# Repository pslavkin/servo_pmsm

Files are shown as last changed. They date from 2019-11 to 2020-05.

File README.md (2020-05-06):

# PMSM Servo motor driver based on C2000 - PCB

> development of a customized high precision microcontrolled permament magnet embedded servo motor

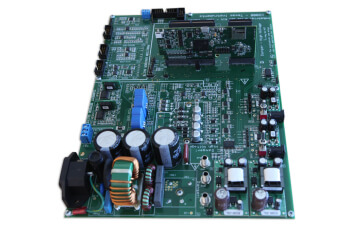
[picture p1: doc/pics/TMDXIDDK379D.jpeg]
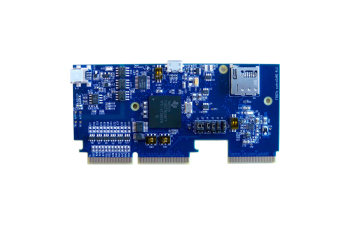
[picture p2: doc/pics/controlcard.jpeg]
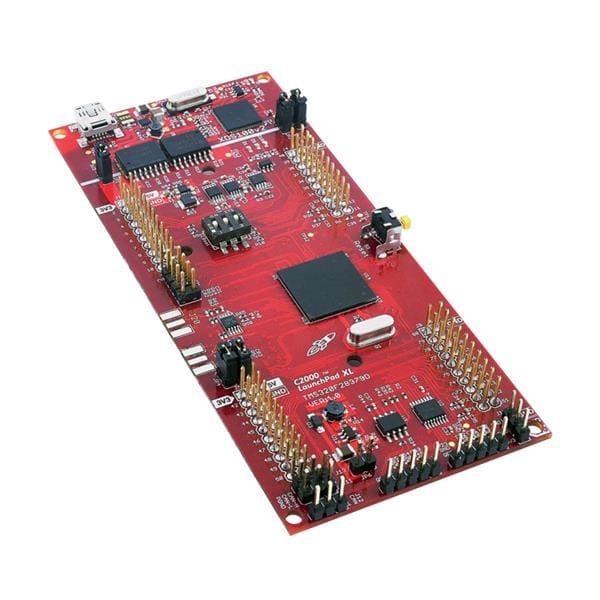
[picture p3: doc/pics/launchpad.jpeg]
   
## Progress
<!--- 
- ![rojo](https://placehold.it/15/FF0000/000000?text=+)
- ![amarillo](https://placehold.it/15/FFFF00/000000?text=+)
- ![azul](https://placehold.it/15/0000FF/000000?text=+)
- ![verde](https://placehold.it/15/00FF00/000000?text=+)
embedded gist
<img src="doc/pics/servo-15.jpg" width="800"/>
https://gist.github.com/rxaviers/7360908

- :heavy_check_mark: connected to a chinise CNC works!
- :red_circle:       Dual core interconnect IPC
-->
- :heavy_check_mark:    controller schematics from Altium to kicad
- :heavy_check_mark:    setting kicad libs, datasheet, remove unused IC's
- :heavy_check_mark:    mixing high power cirtuit to kicad
- :heavy_check_mark:    two servo motor control on same board aproach!
- :heavy_check_mark:    setting kicad libs, datasheet, remove unused IC's 
- :heavy_check_mark:    adc
- :heavy_check_mark:    igbt interface
- :heavy_check_mark:    lem measurement
- :heavy_check_mark:    ac input
- :heavy_check_mark:    connect interfaces to GPIO's (ecat0/1, enet, leds, etc)
- :heavy_check_mark:    shunt using isolated ADC fron/backend
- :heavy_check_mark:    isolated GPI for external switches and sensor on any polarity
- :heavy_check_mark:    8 channel buffer to drive IGBT
- :heavy_check_mark:    ac/dc -> dc/dc -> ldo for clean power supplies
- :heavy_check_mark:        Line voltage measurement
- :heavy_check_mark:        overcurrent protection using CMPSS
- :red_circle:          aborted! lem is better changing/adding shunt measurement with sigma deltas isolated ADC
- :heavy_check_mark:    LEM revival. I've decided to return to the idea of LEM 'cose sigma
  delta carry more complexity and less benefits. But SD could be included on power stage and
I'll let pins to aquire and filter it.
- :heavy_check_mark:     schematics ready!, and check rules passed. go to part numbering and
  footprint selection
- :red_circle:          isolated GPIO aborted! I've reise free pins that comes from IGBT
- :heavy_check_mark:    EVE LCD driven choosen as the UI by spi.. I's all the thinks we need
- :heavy_check_mark:    3d added EVE LCD 3. 20w offline ac/dc changed to 10w. 15vcold
  eliminated, two buttons eliminated. 2 LEM's eliminated
- :construction:        all footprints choosen, but deserves some comprobation
- :heavy_check_mark:    placement rought done
- :heavy_check_mark:    ronting..
- :heavy_check_mark:    moving ethernet connector to right and remove 15vh->5vh and debuh
- :heavy_check_mark:    ronting DONE!!! begin to improve nets..
- :heavy_check_mark:    Gerbers READY.. leaving Moldova...
- :heavy_check_mark:    Gerbers RELOADED from Bariloche
- :heavy_check_mark:    Gerbers RELEAED ... cross fingers..
- :heavy_check_mark:    Board partially manufactured!! miss uC that is traveling on a
  boat...see pics

## Welcome back Moldova 3.0

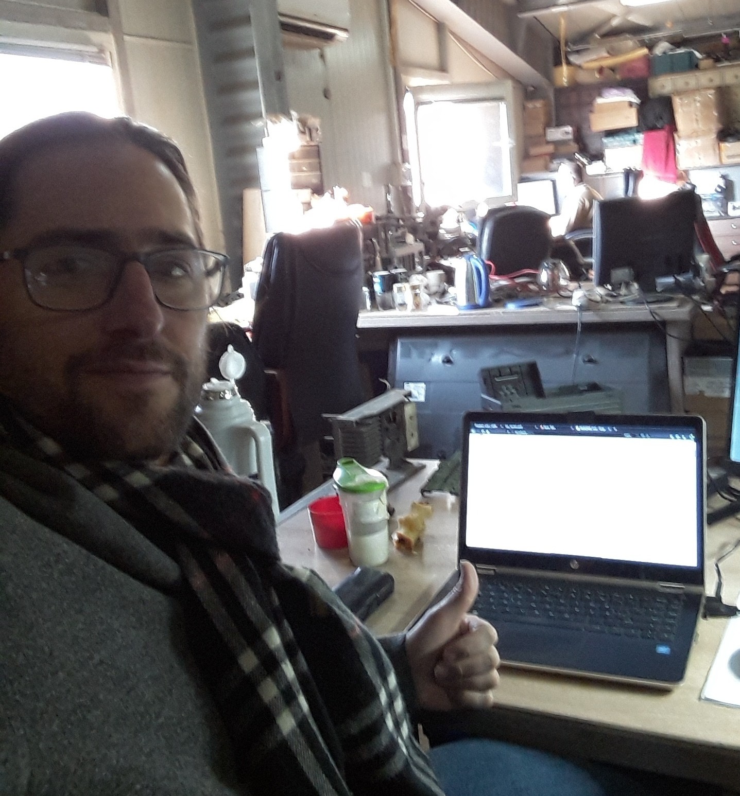
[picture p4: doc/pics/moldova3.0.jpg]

I've come back to finish PCB, there we are... sdarobia!

## Table of Contents

- [schematics](#schematics)
- [Contributing](#contributing)
- [Team](#team)
- [FAQ](#faq)
- [Support](#support)
- [Hierarchy](#hierarchy)
- [License](#license)
---
## schematics
There are the actual schematics generated until now:

## complete pdf link
[complete pdf schematic](./doc/pics/servo.pdf)

## Layout
Met's begin with layout!
first pic, easy, doesn't it?

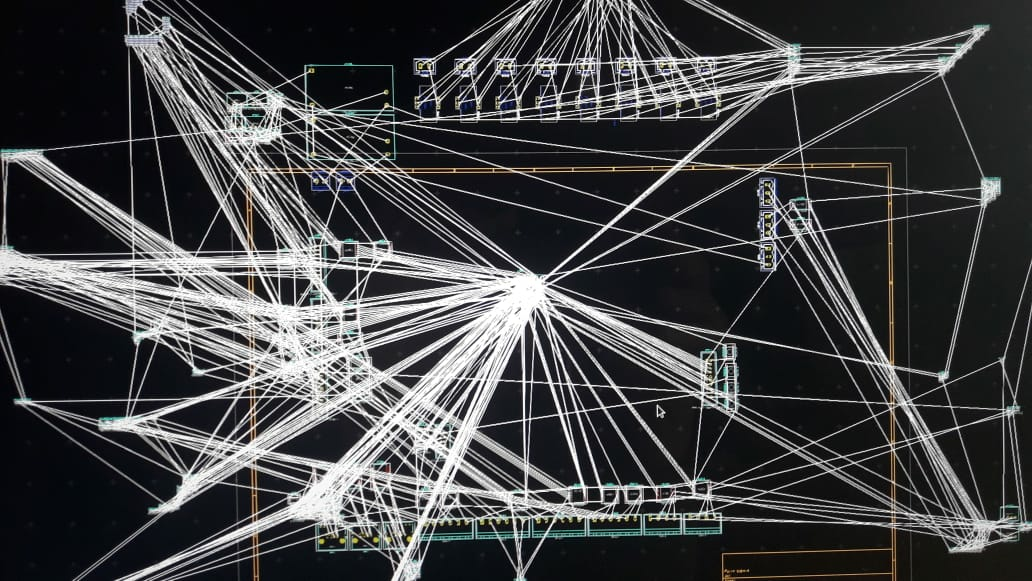
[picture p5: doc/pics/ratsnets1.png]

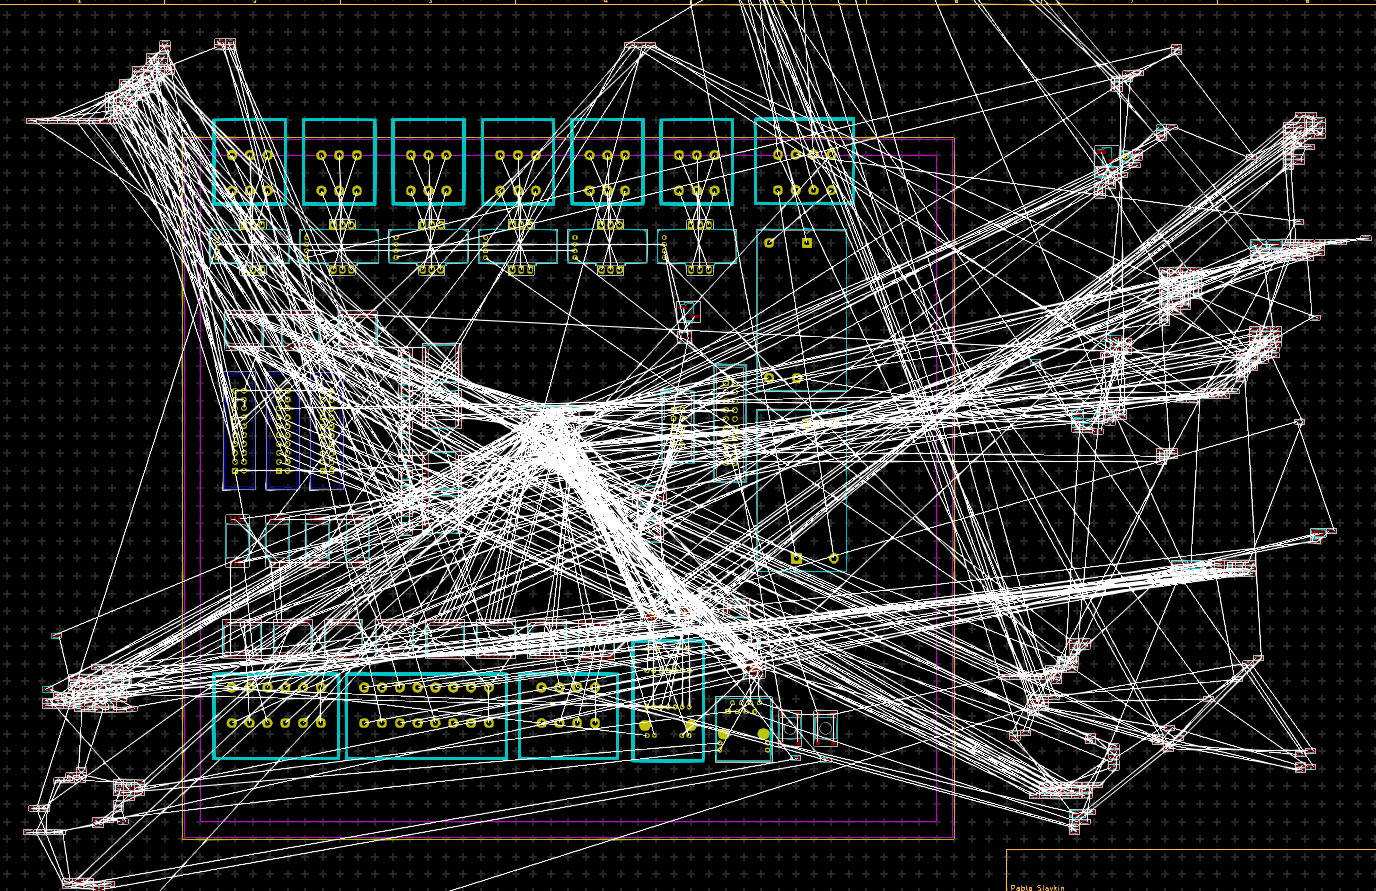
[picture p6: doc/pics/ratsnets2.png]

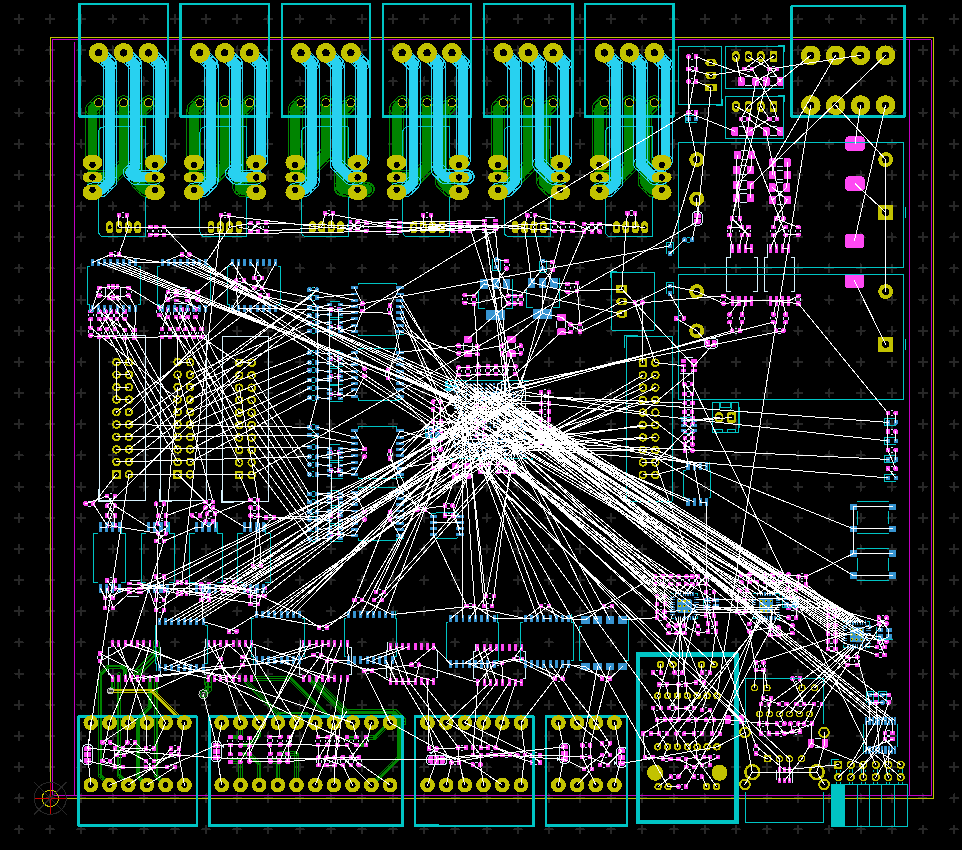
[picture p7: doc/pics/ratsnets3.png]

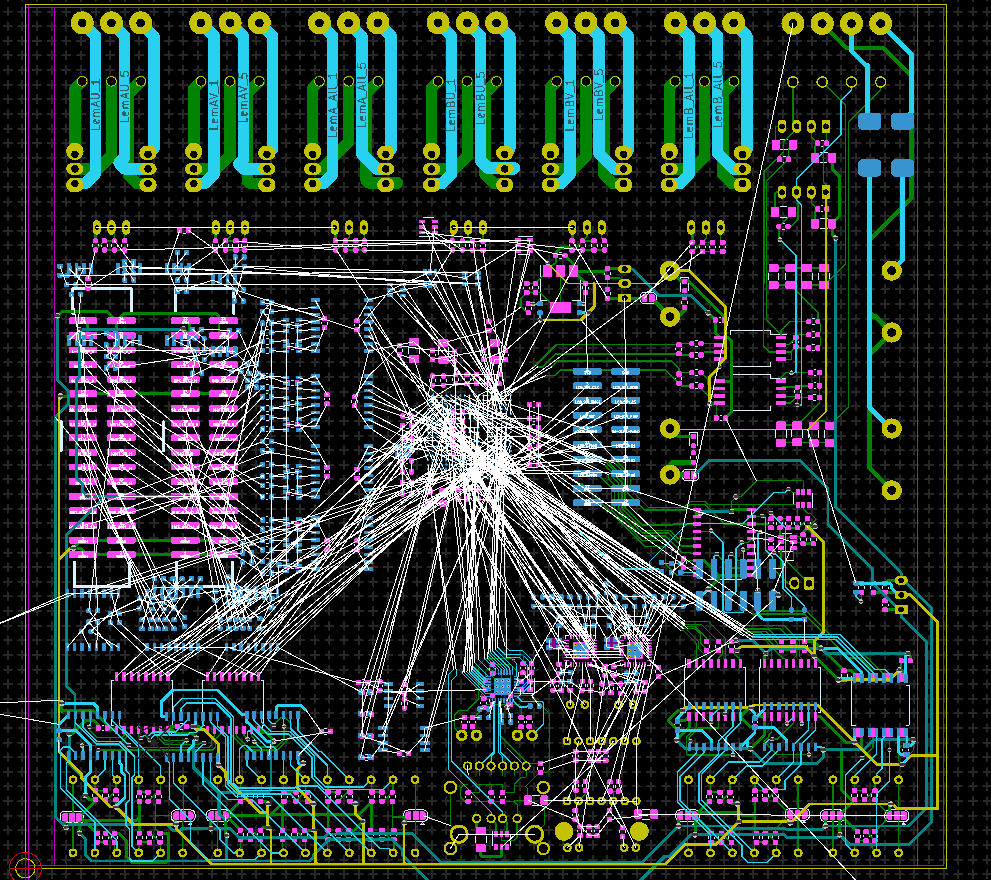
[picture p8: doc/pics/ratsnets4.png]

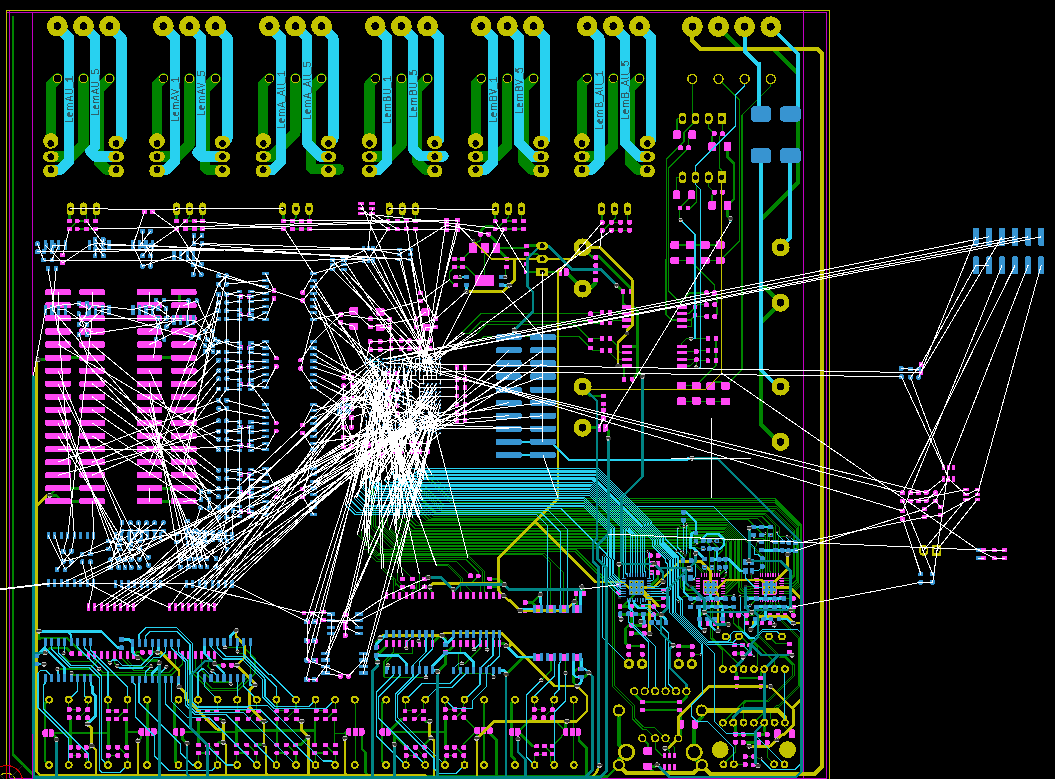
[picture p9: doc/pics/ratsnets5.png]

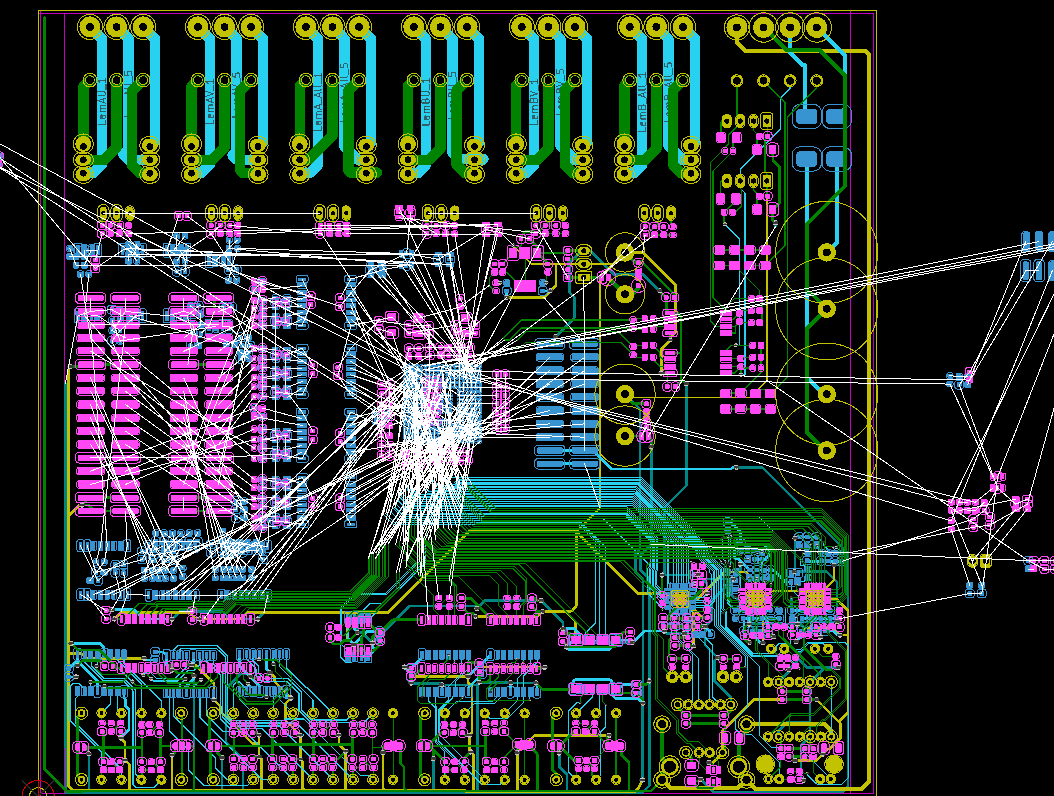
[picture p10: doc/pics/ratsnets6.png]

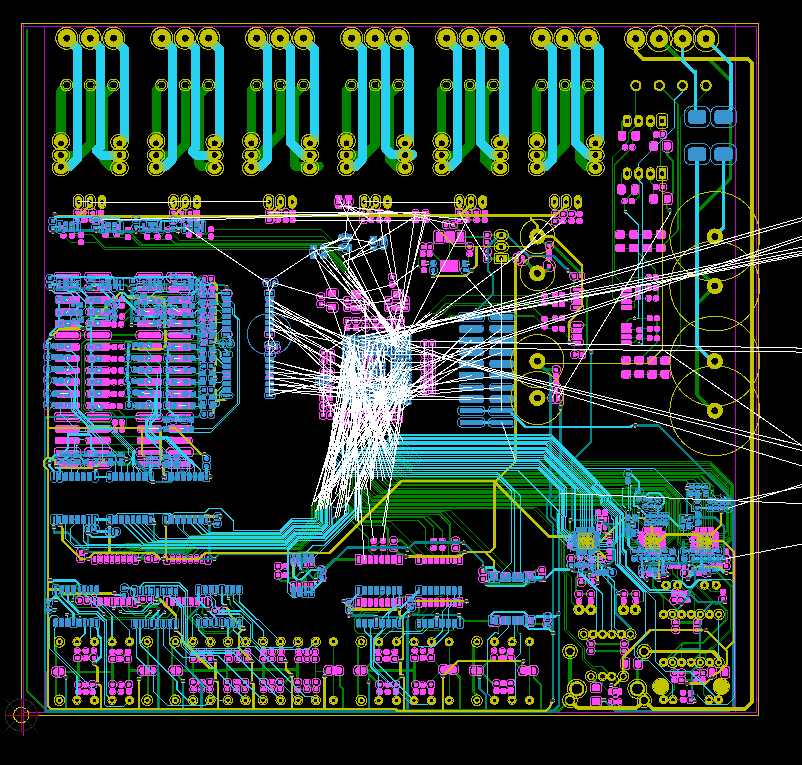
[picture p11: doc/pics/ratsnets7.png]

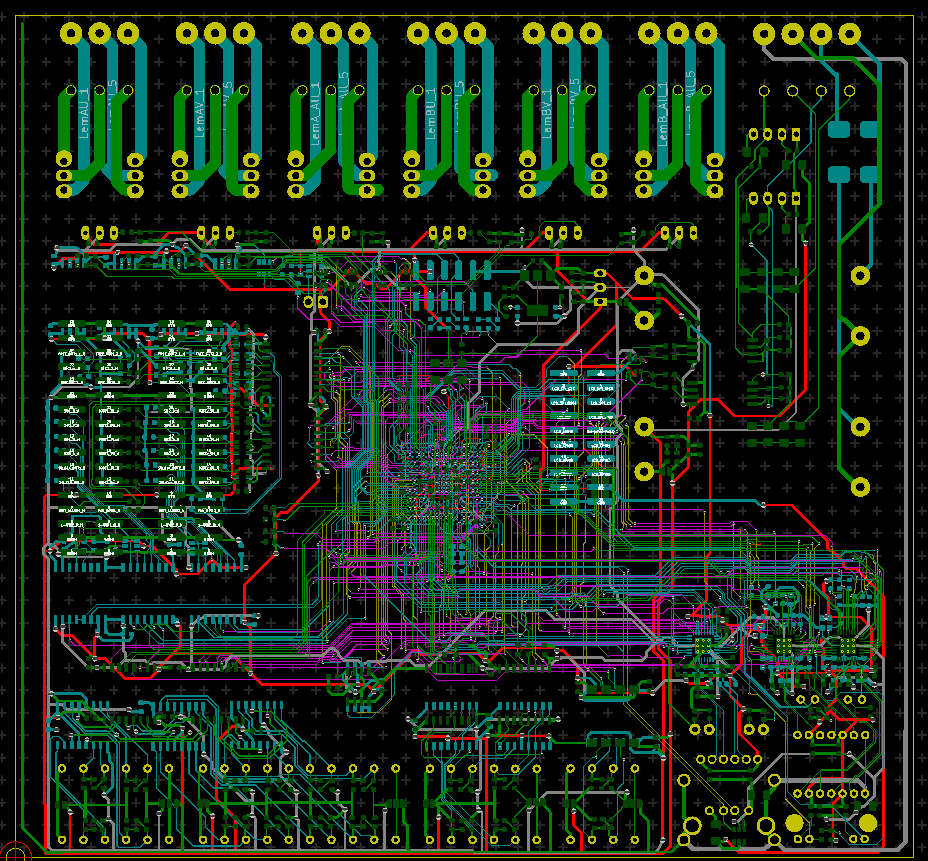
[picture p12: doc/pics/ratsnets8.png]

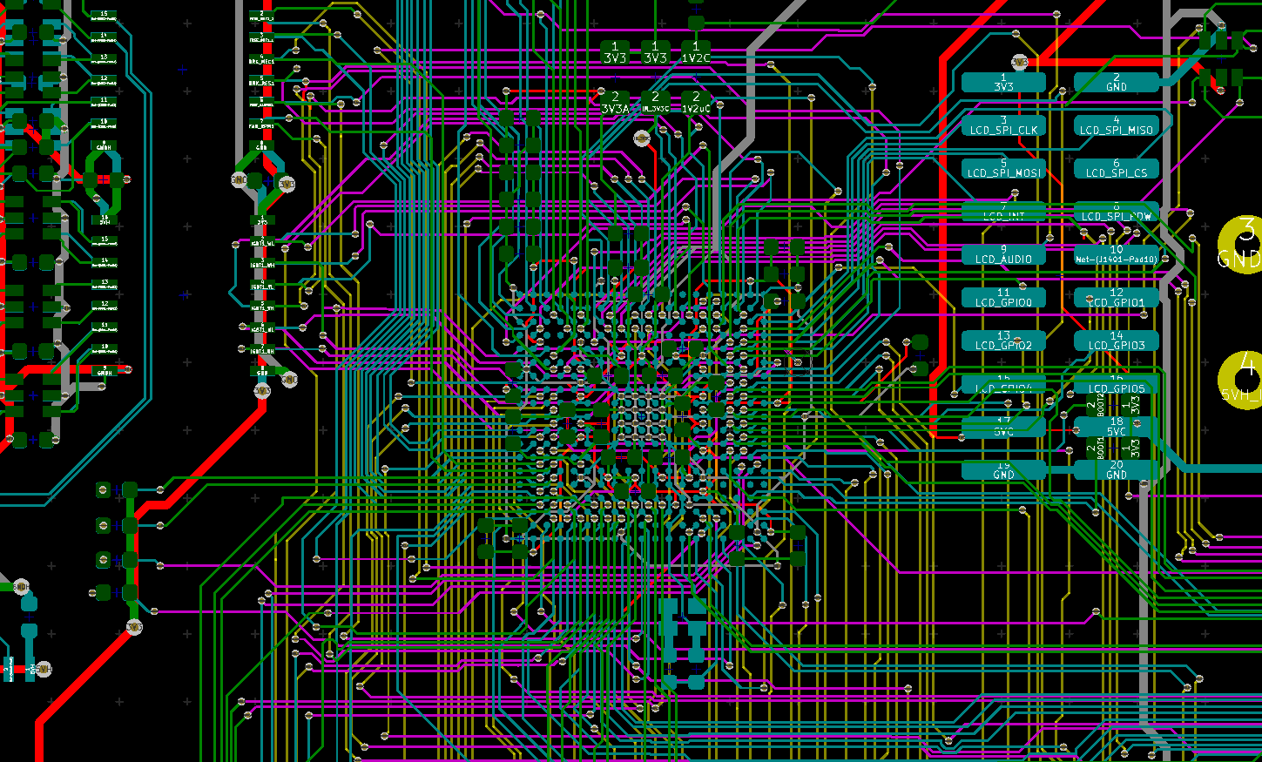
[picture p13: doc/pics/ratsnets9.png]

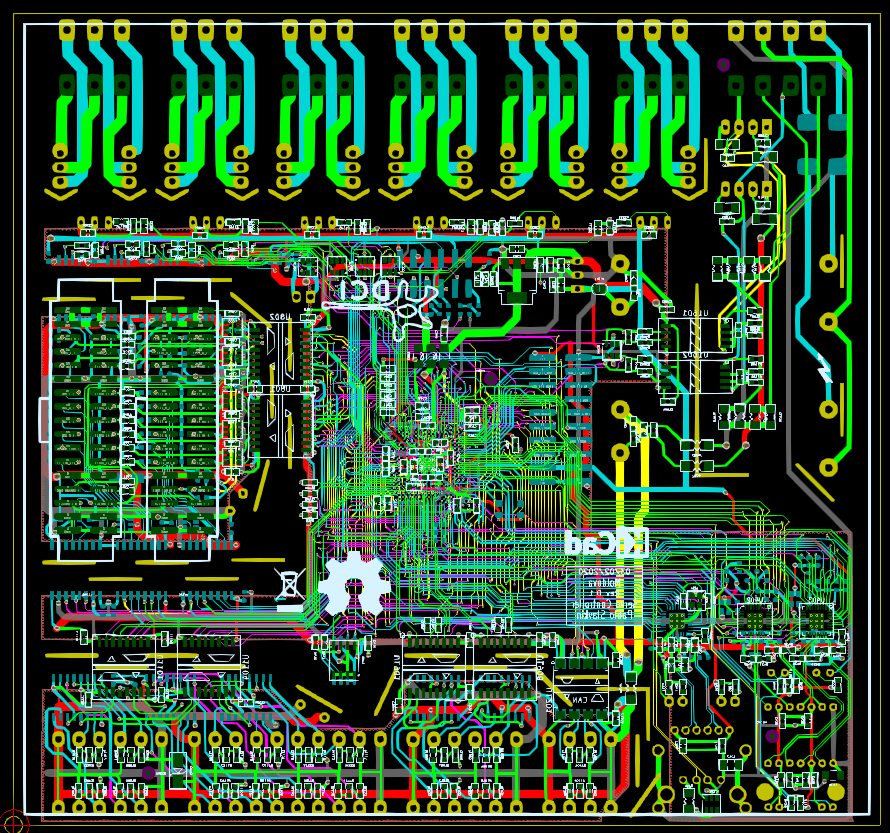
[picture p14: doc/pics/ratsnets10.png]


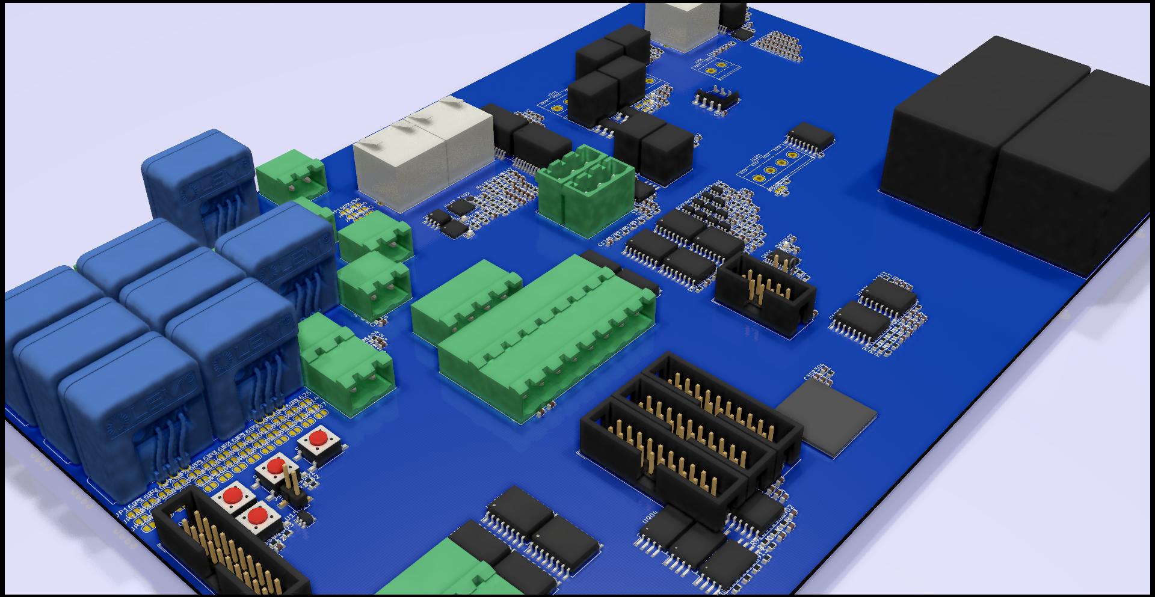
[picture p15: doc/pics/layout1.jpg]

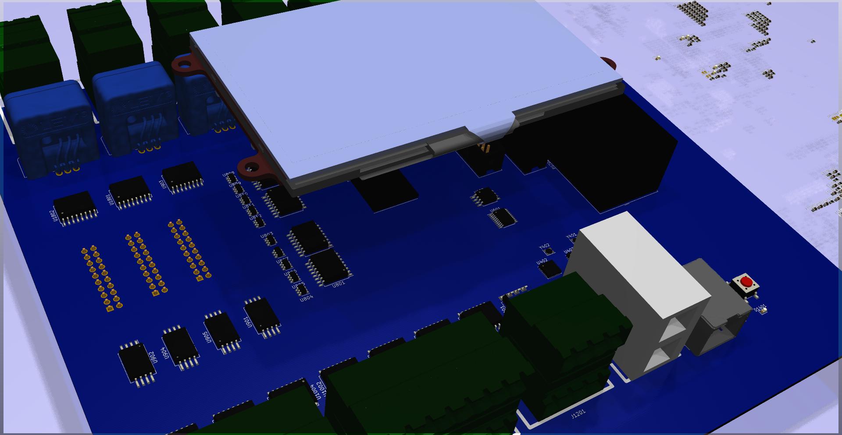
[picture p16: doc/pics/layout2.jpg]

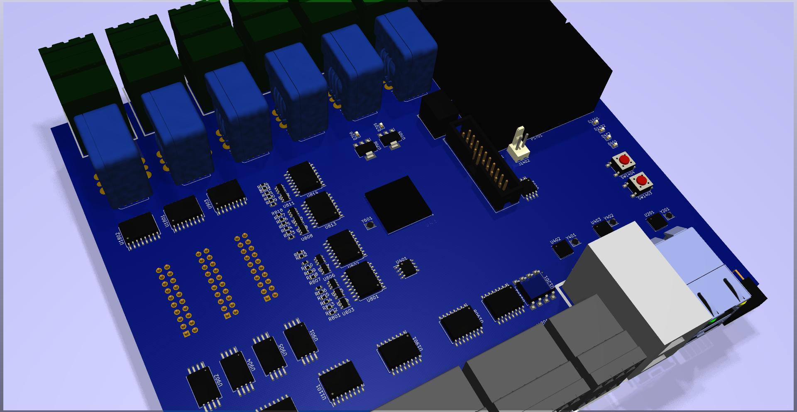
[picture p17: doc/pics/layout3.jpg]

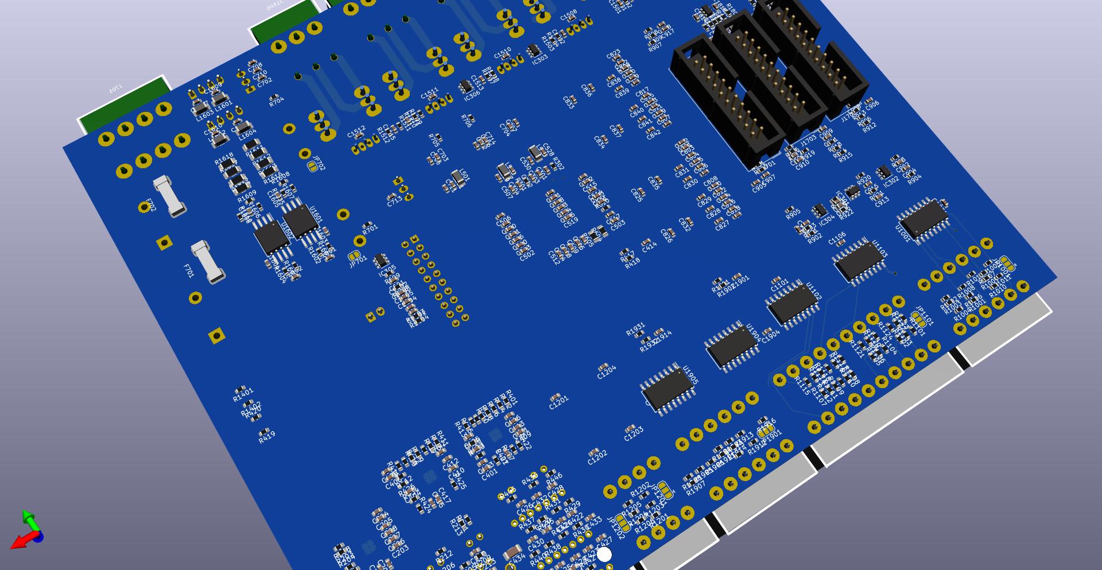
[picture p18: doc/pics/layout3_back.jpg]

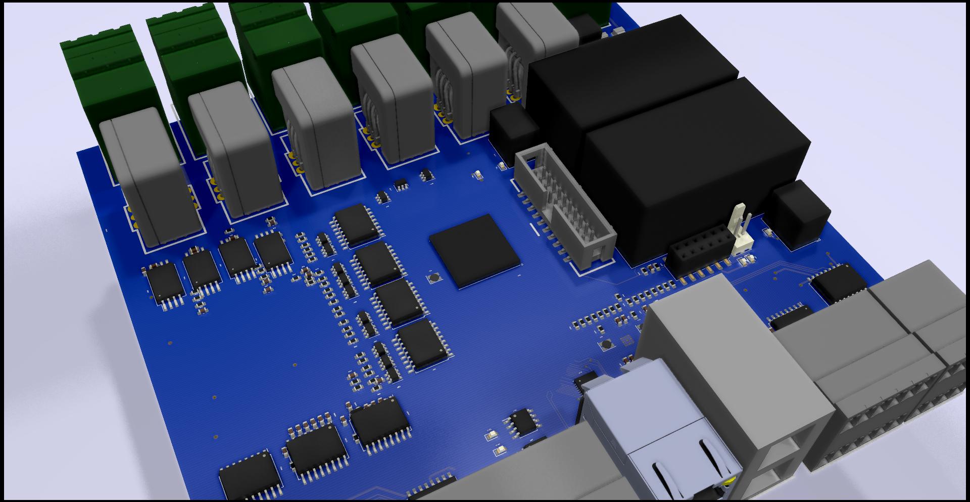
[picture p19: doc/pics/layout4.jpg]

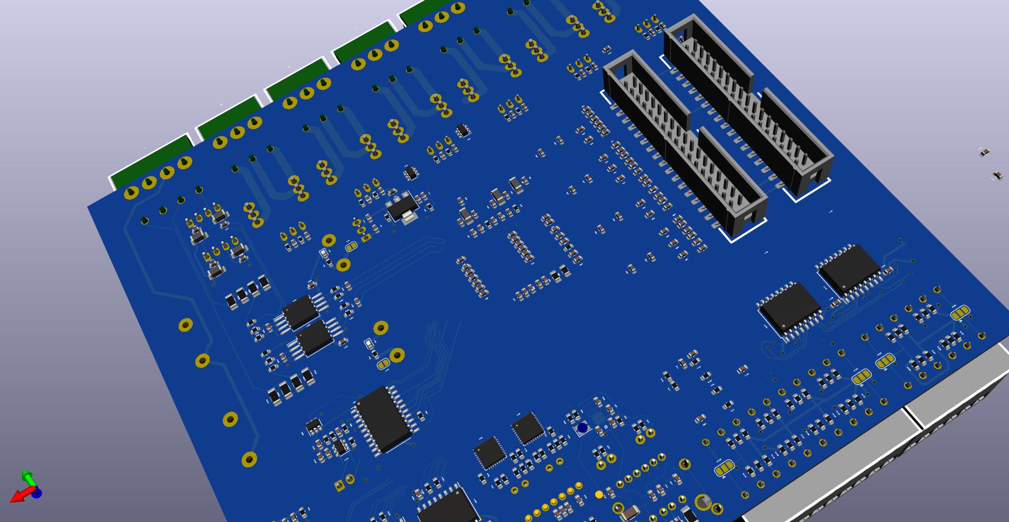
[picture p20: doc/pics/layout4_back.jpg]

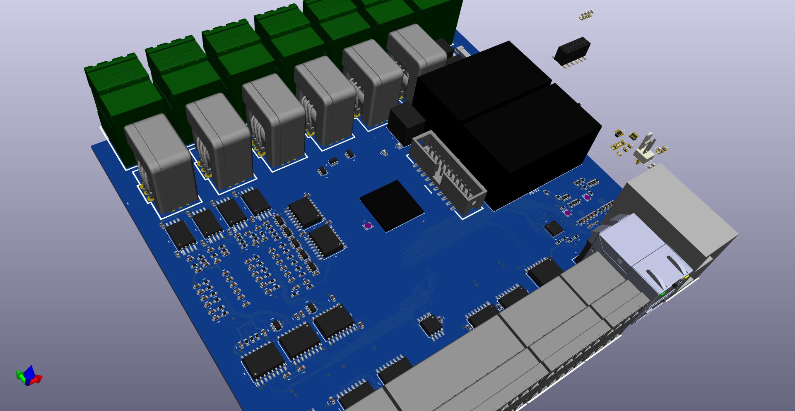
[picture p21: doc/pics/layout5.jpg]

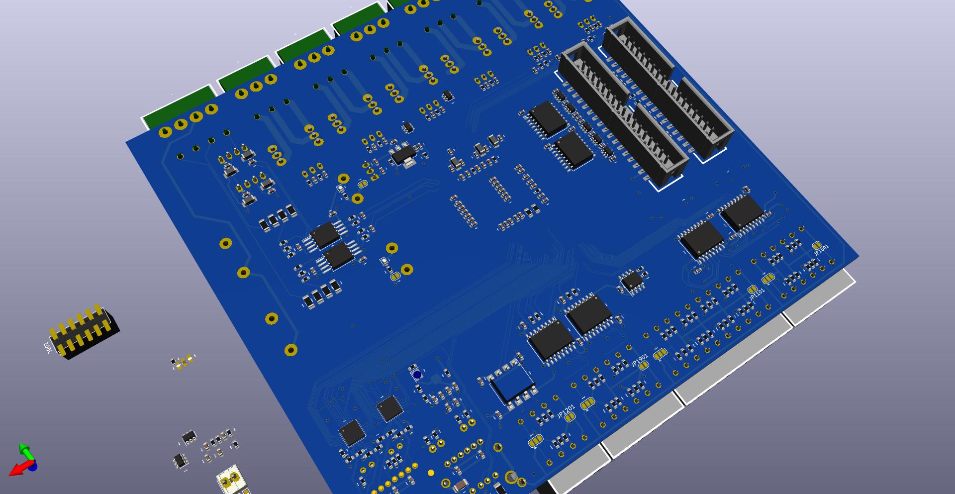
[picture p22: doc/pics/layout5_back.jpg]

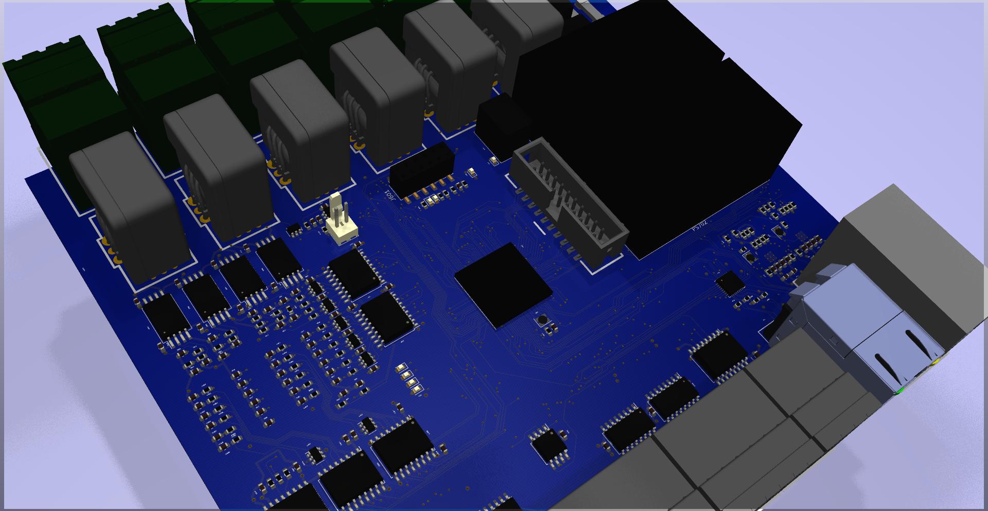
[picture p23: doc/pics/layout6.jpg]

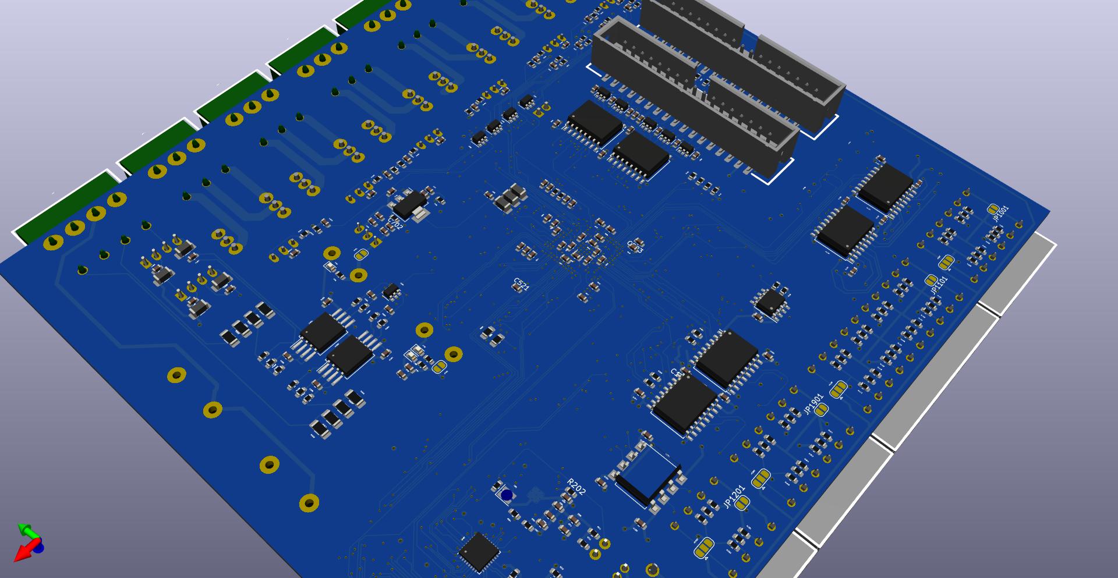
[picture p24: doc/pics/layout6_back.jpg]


## A mounting optional case shape
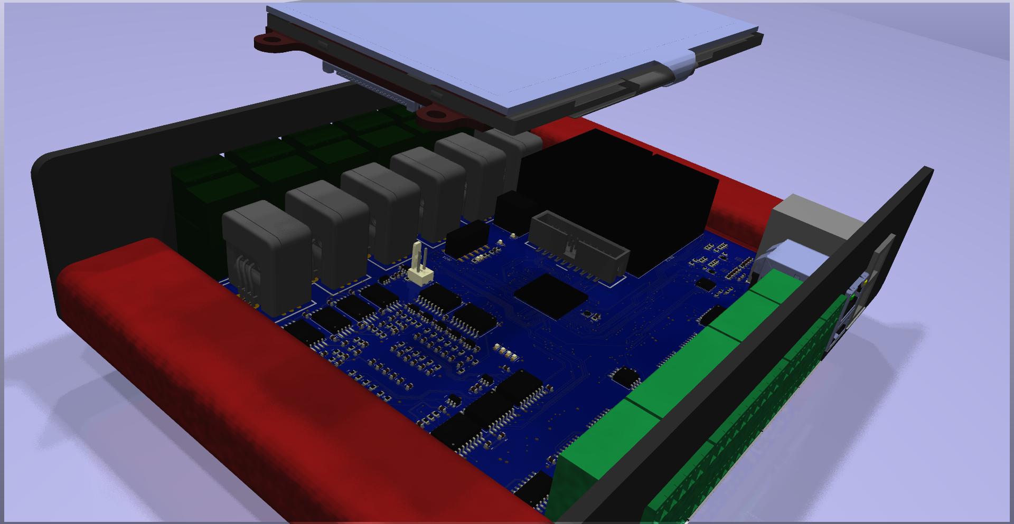
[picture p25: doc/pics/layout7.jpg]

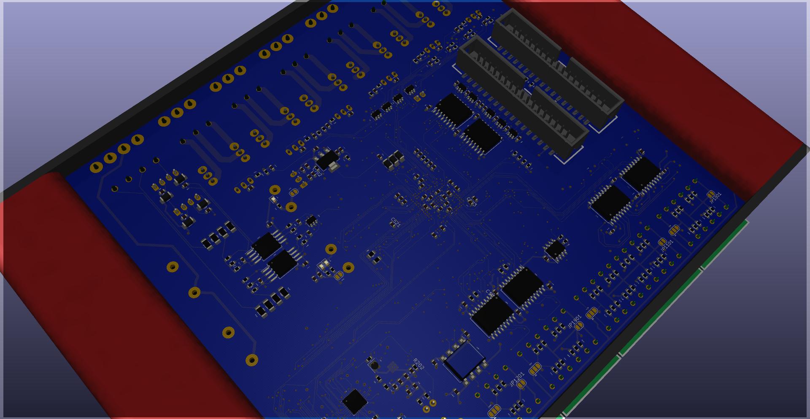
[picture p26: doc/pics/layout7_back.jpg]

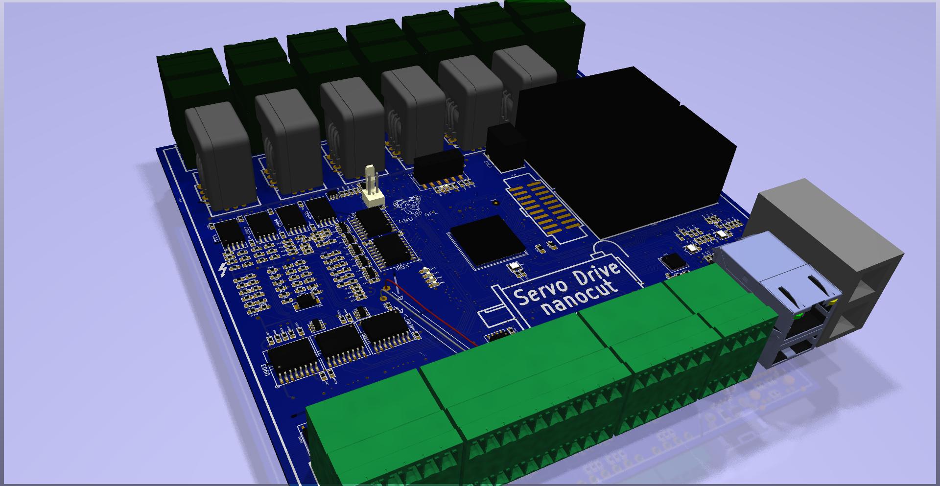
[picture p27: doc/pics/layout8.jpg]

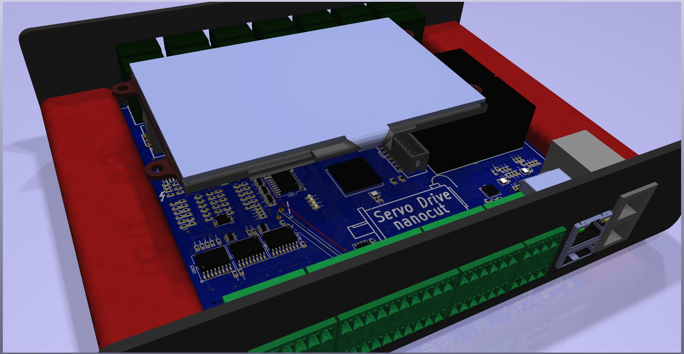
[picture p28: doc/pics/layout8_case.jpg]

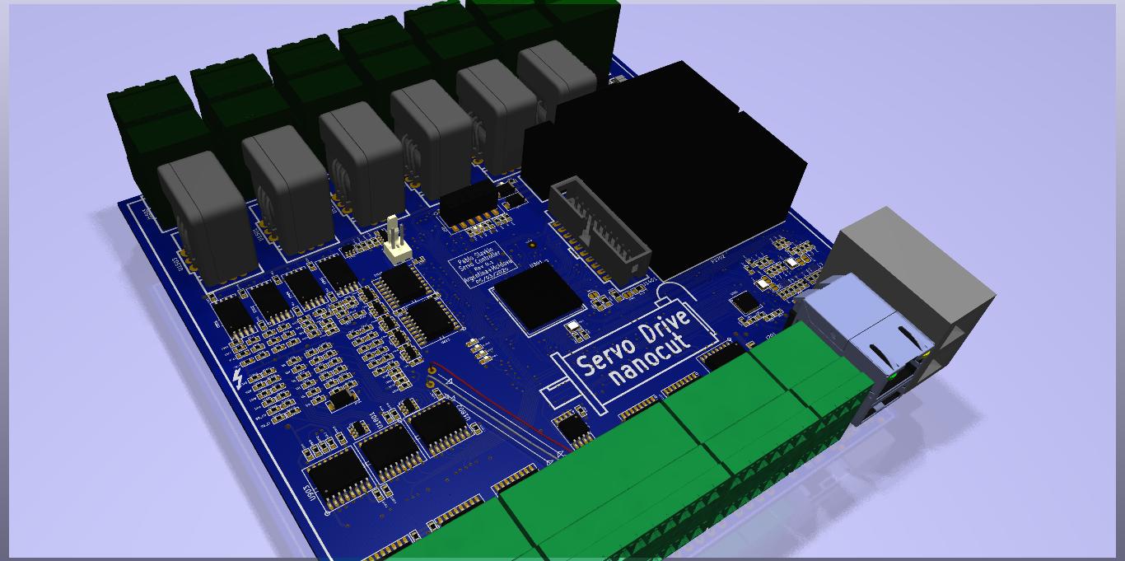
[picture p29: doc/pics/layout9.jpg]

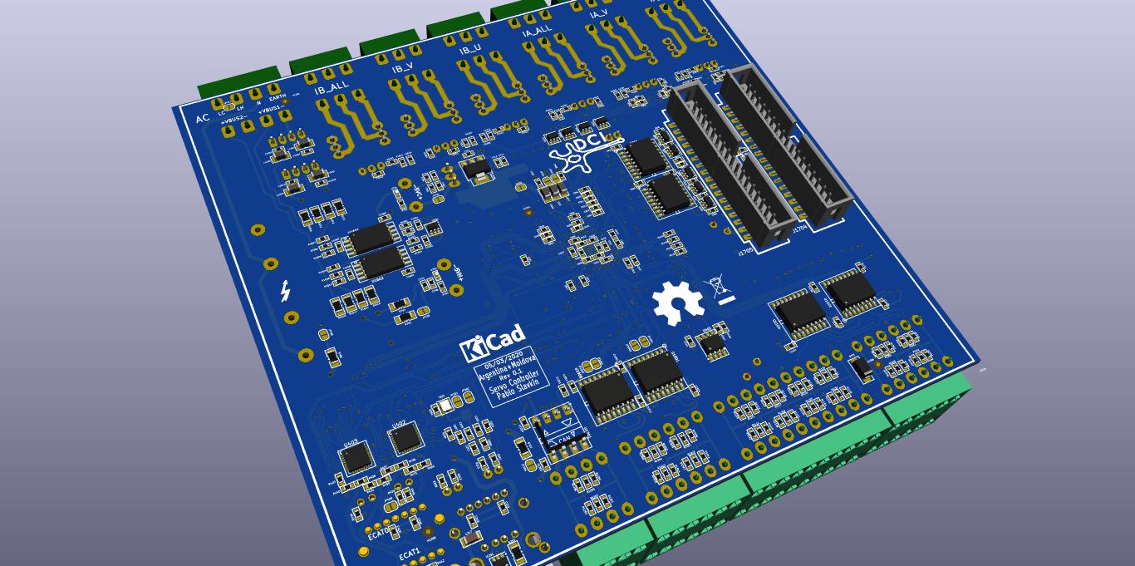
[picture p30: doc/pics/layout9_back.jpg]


## Nets plane 2d and 3d nets
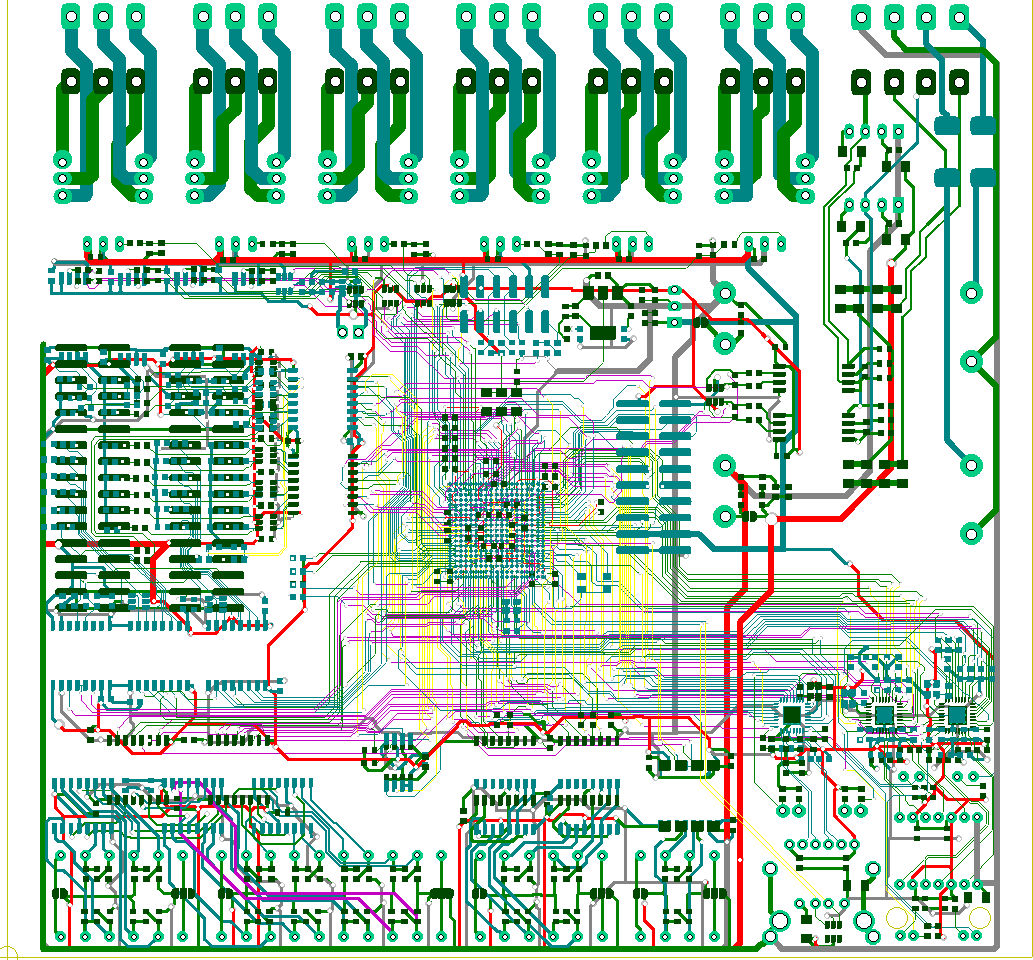
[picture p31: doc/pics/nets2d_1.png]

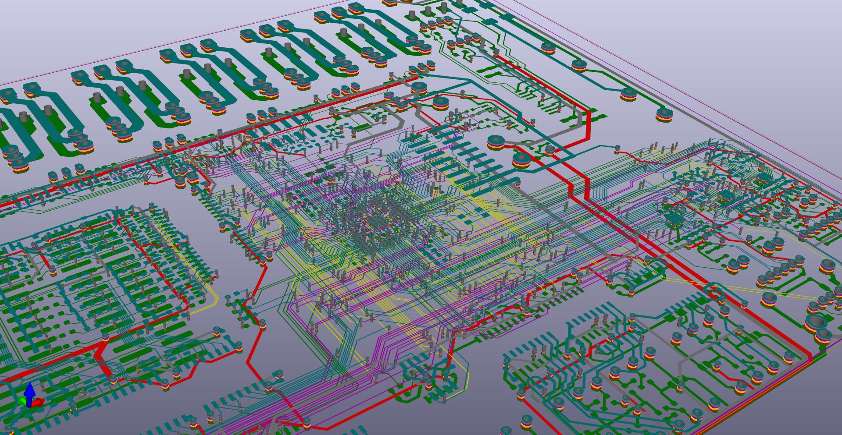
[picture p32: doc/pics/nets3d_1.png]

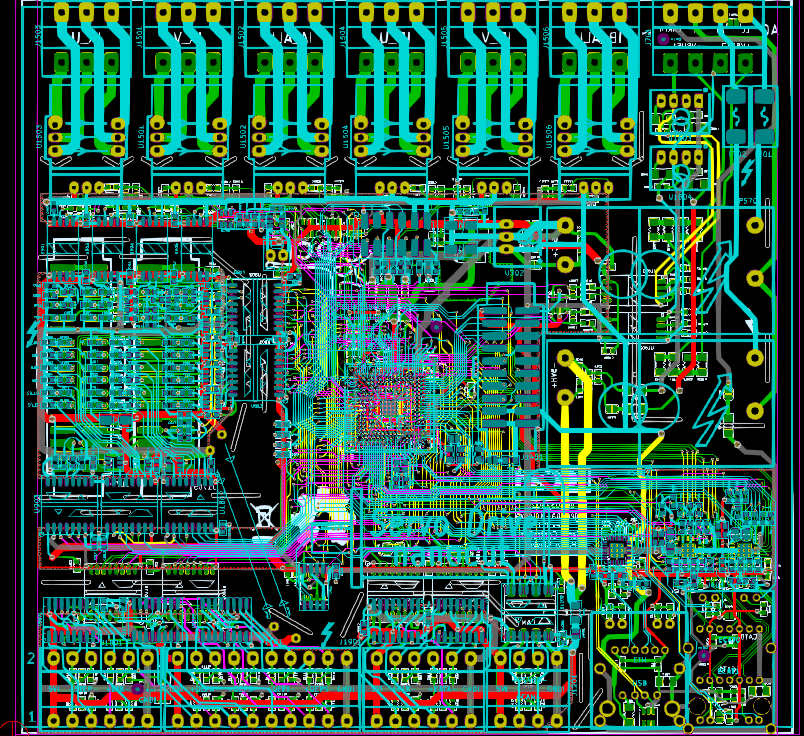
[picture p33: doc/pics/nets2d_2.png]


## Video 3d rotating PCB


## schematic in pics

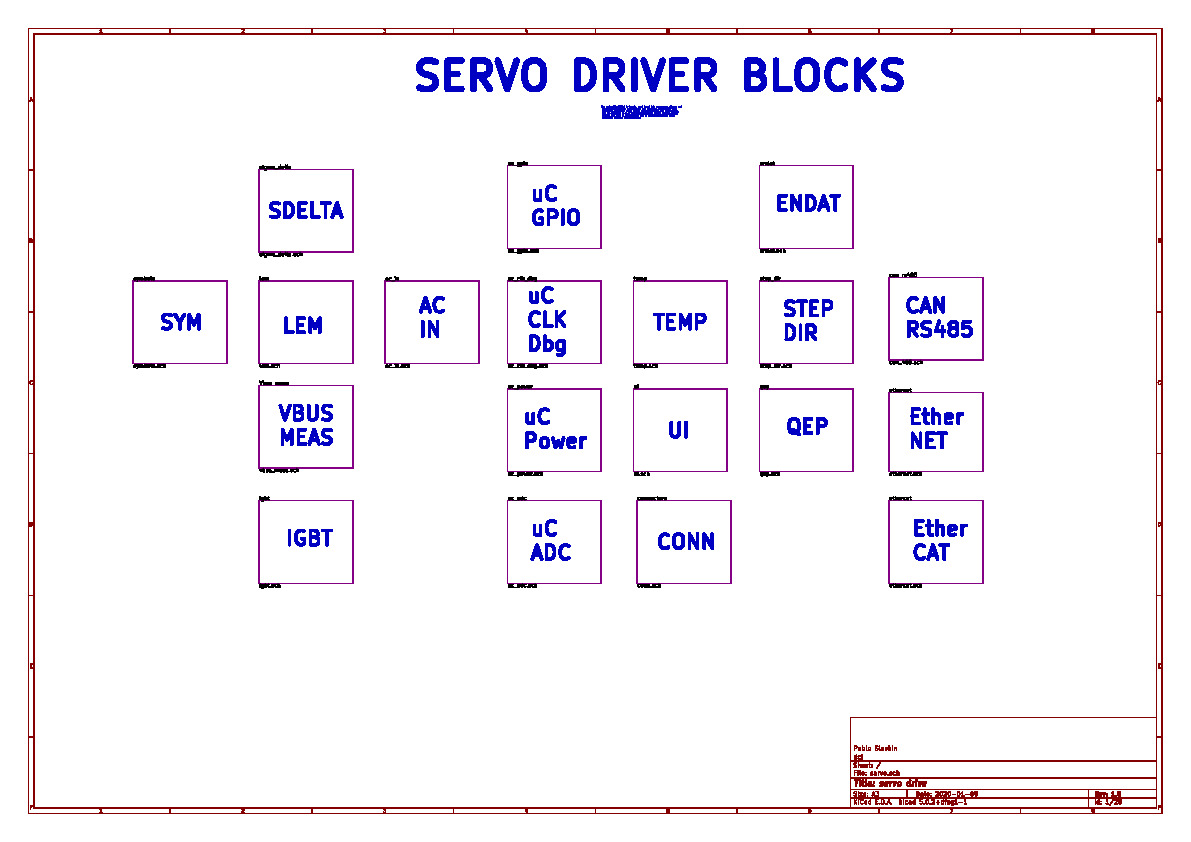
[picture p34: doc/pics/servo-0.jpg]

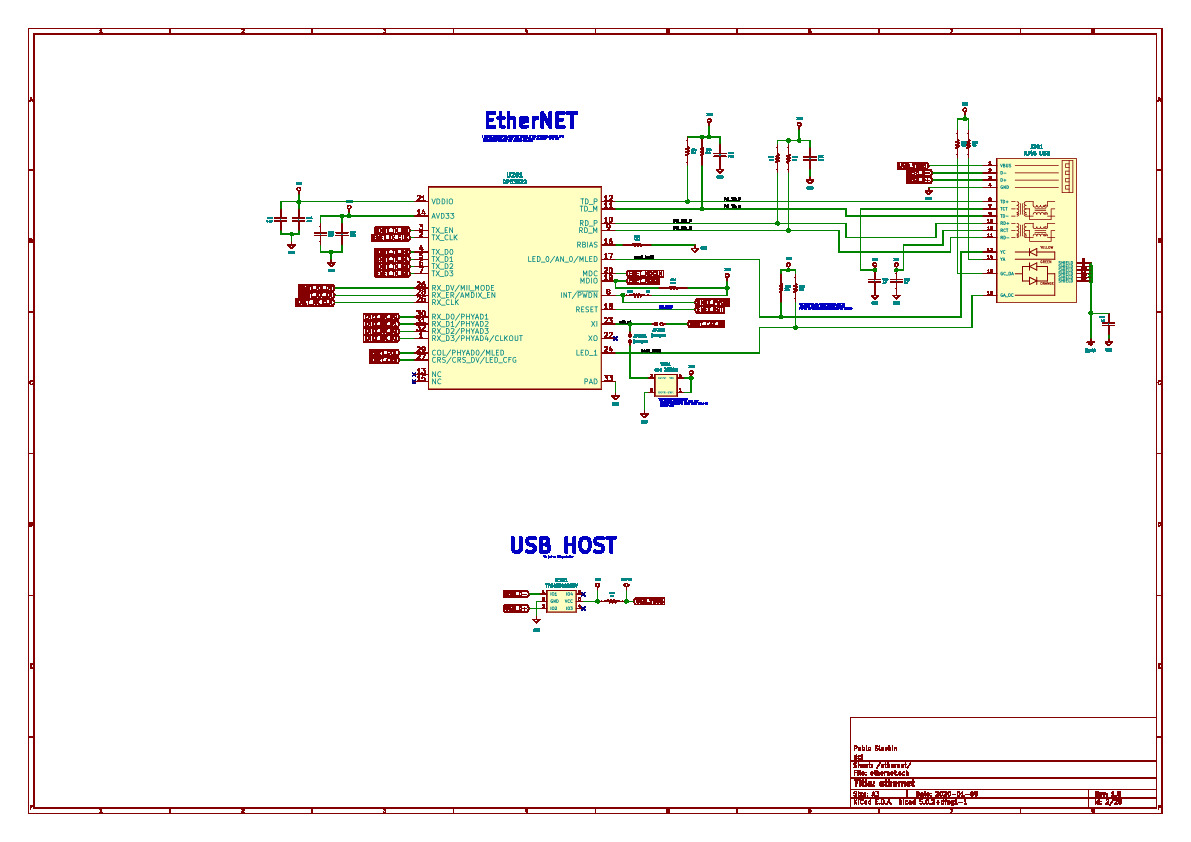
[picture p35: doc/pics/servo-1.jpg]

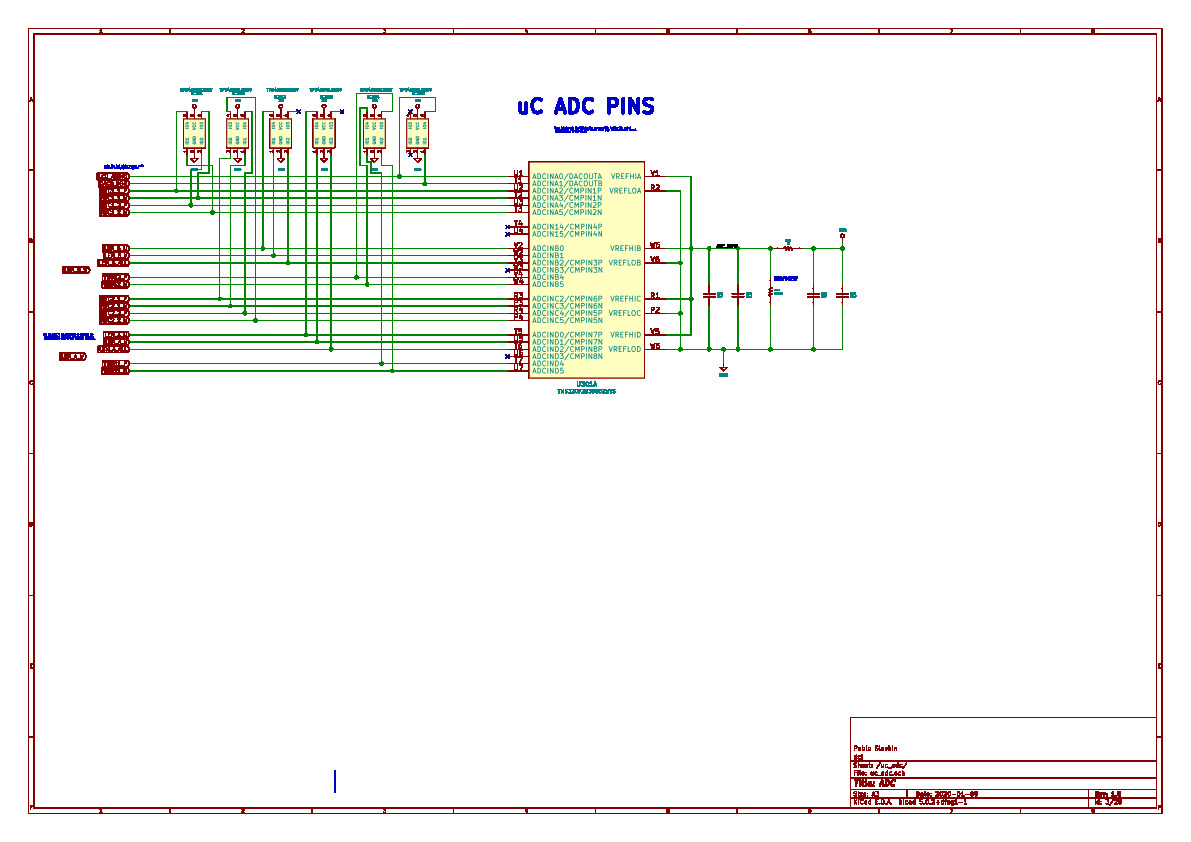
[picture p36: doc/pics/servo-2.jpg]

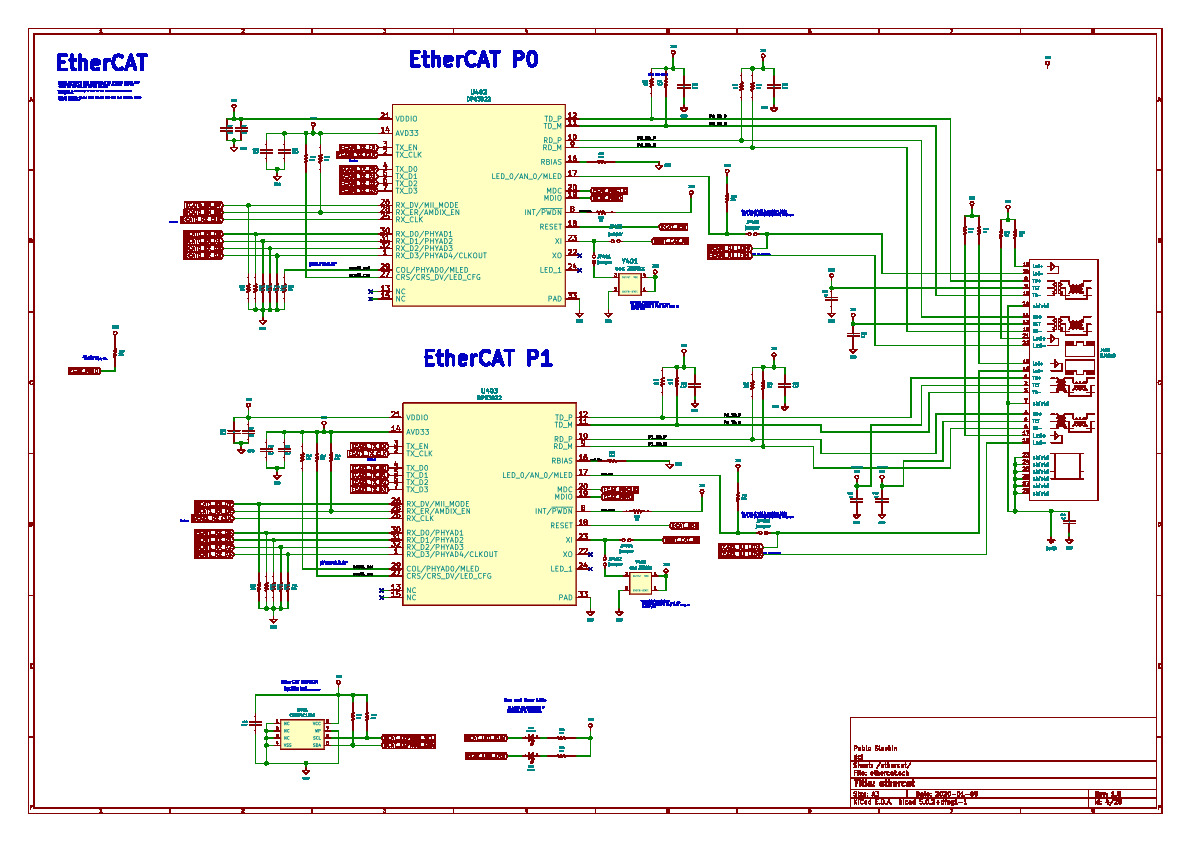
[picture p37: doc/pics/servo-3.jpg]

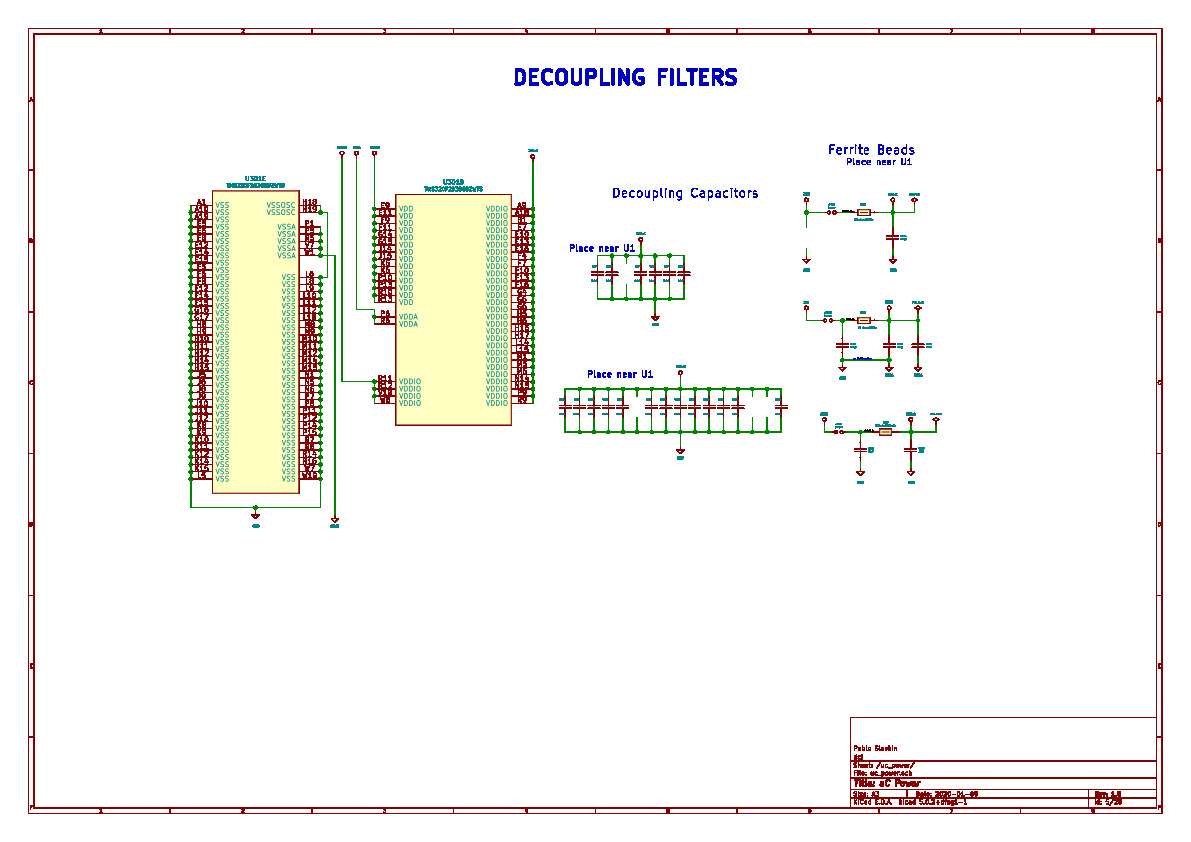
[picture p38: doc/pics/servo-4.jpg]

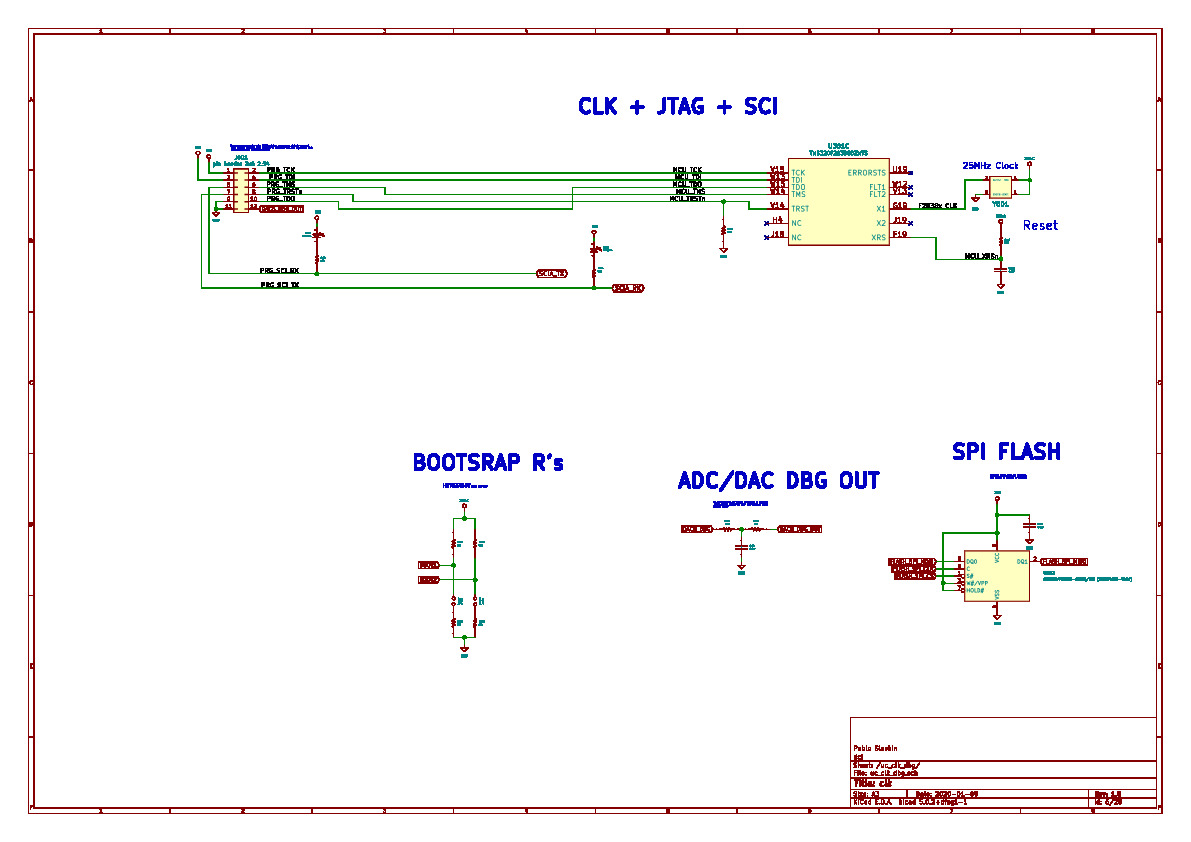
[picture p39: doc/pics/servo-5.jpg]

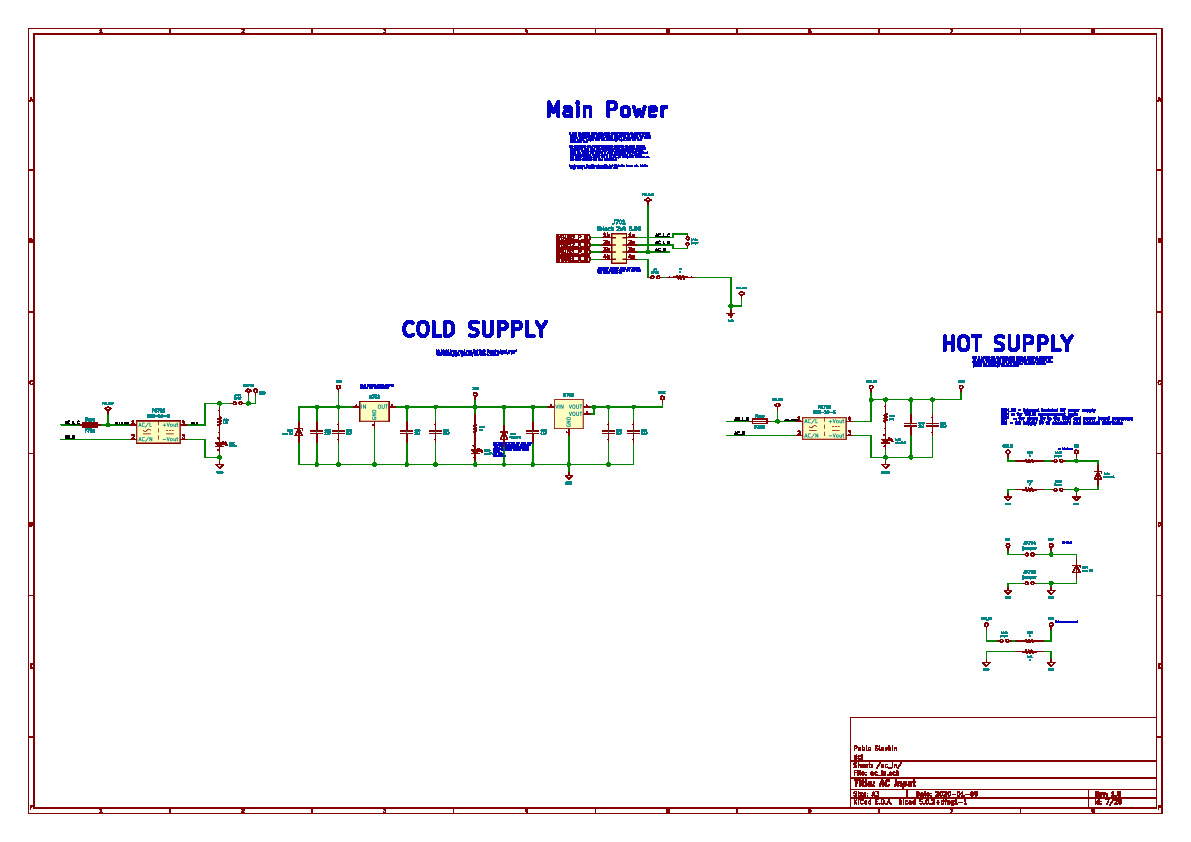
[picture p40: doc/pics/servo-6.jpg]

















## Manufactured PCB

I wanna cry! 













## Hierarchy

<!-- tree --ignore-case -L 3 -I "*utils*|*user*|*target*|*Debug*|Release|include|driverlib|tags|*types_c*" -->

```ruby

```

<!--

## Features
## Usage (Optional)
## Documentation (Optional)
## Tests (Optional)

- Going into more detail on code and technologies used
- I utilized this nifty <a href="https://github.com/adam-p/markdown-here/wiki/Markdown-Cheatsheet" target="_blank">Markdown Cheatsheet</a> for this sample `README`.

## Contributing

## Team

| <a href="https://github.com/pslavkin" target="_blank">**pslavkin**</a> | <a href="https://github.com/pslavkin" target="_blank">**neo**</a> | <a href="https://github.com/pslavkin" target="_blank">**doe**</a> |
| :---: |:---:| :---:|
| [![pslavkin](https://avatars1.githubusercontent.com/u/8507601?s=150)](https://github.com/pslavkin) | [<img src=https://media.metrolatam.com/2019/04/04/matrixreloadedneo01-3ec18ba895c91e664865ece4b3c9381d-600x400.jpg width="200" height="150">](https://github.com/pslavkin) | [<img src="https://encrypted-tbn0.gstatic.com/images?q=tbn:ANd9GcStNOGY8Cj2fH3B6L3OD91VJiuIq3iBA3FkCz0w0OJSQGuIxrsF" width="200" height="150">](https://github.com/pslavkin)  |
| <a href="https://github.com/pslavkin" target="_blank">`github.com/pslavkin`</a> | <a href="https://github.com/pslavkin" target="_blank">`github.com/pslavkin`</a> | <a href="https://github.com/pslavkin" target="_blank">`github.com/pslavkin`</a> |

## Support

Reach out to me at one of the following places!
- <a href="http://www.ti.com/tool/launchXL-F28379d#" target="_blank">**launchXL-F28379d** <img src="doc/pics/launchpad.jpeg"    title="launchpad"   width="100" height="100" alt="launchpad"></a>

## License

[![License](http://img.shields.io/:license-mit-blue.svg?style=flat-square)](http://badges.mit-license.org)

- **[MIT license](http://opensource.org/licenses/mit-license.php)**
- Copyright 2019 © <a href="http://fvcproductions.com" target="_blank">FVCproductions</a>.

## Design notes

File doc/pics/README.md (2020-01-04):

# PMSM Servo motor driver based on C2000 - PCB

> development of a customized high precision microcontrolled permament magnet embedded servo motor

   
## Progress
<!--- 
- ![rojo](https://placehold.it/15/FF0000/000000?text=+)
- ![amarillo](https://placehold.it/15/FFFF00/000000?text=+)
- ![azul](https://placehold.it/15/0000FF/000000?text=+)
- ![verde](https://placehold.it/15/00FF00/000000?text=+)
embedded gist
<img src="doc/pics/servo-15.jpg" width="800"/>
https://gist.github.com/rxaviers/7360908

- :heavy_check_mark: connected to a chinise CNC works!
- :red_circle:       Dual core interconnect IPC
-->
- :heavy_check_mark:    controller schematics from Altium to kicad
- :construction:        setting kicad libs, datasheet, remove unused IC's
- :construction:        mixing high power cirtuit to kicad
- :construction:        two servo motor control on same board aproach!
- :construction:        setting kicad libs, datasheet, remove unused IC's 
- :heavy_check_mark:    adc
- :heavy_check_mark:    igbt interface
- :heavy_check_mark:    lem measurement
- :heavy_check_mark:    ac input
- :heavy_check_mark:    connect interfaces to GPIO's (ecat0/1, enet, leds, etc)
- :heavy_check_mark:    shunt using isolated ADC fron/backend
- :heavy_check_mark:    isolated GPI for external switches and sensor on any polarity
- :heavy_check_mark:    8 channel buffer to drive IGBT
- :heavy_check_mark:    ac/dc -> dc/dc -> ldo for clean power supplies
- :construction:        Line voltage measurement
- :construction:        overcurrent protection using CMPSS
- :red_circle:          aborted! lem is better changing/adding shunt measurement with sigma deltas isolated ADC
- :heavy_check_mark:    LEM revival. I've decided to return to the idea of LEM 'cose sigma
  delta carry more complexity and less benefits. But SD could be included on power stage and
I'll let pins to aquire and filter it.

---
## Table of Contents

- [schematics](#schematics)
- [Contributing](#contributing)
- [Team](#team)
- [FAQ](#faq)
- [Support](#support)
- [Hierarchy](#hierarchy)
- [License](#license)
---
## schematics
There are the actual schematics generated until now:








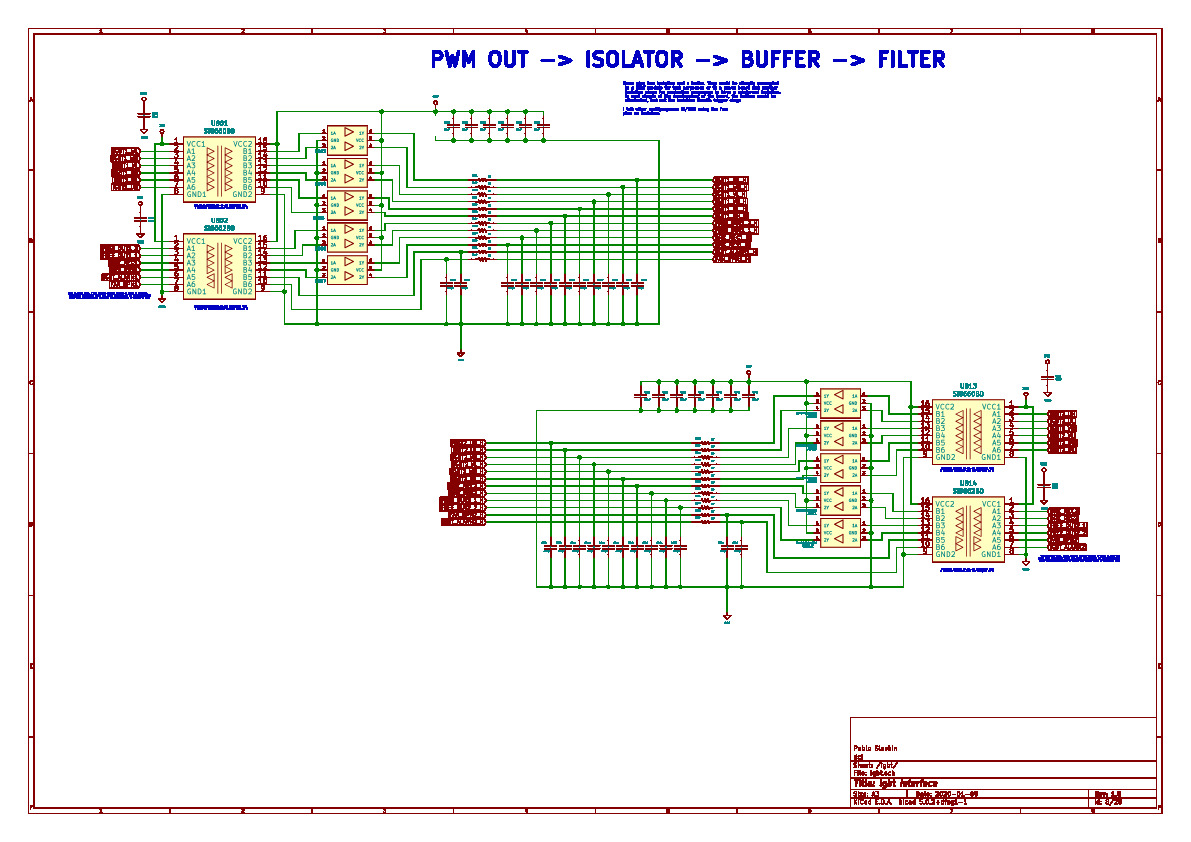
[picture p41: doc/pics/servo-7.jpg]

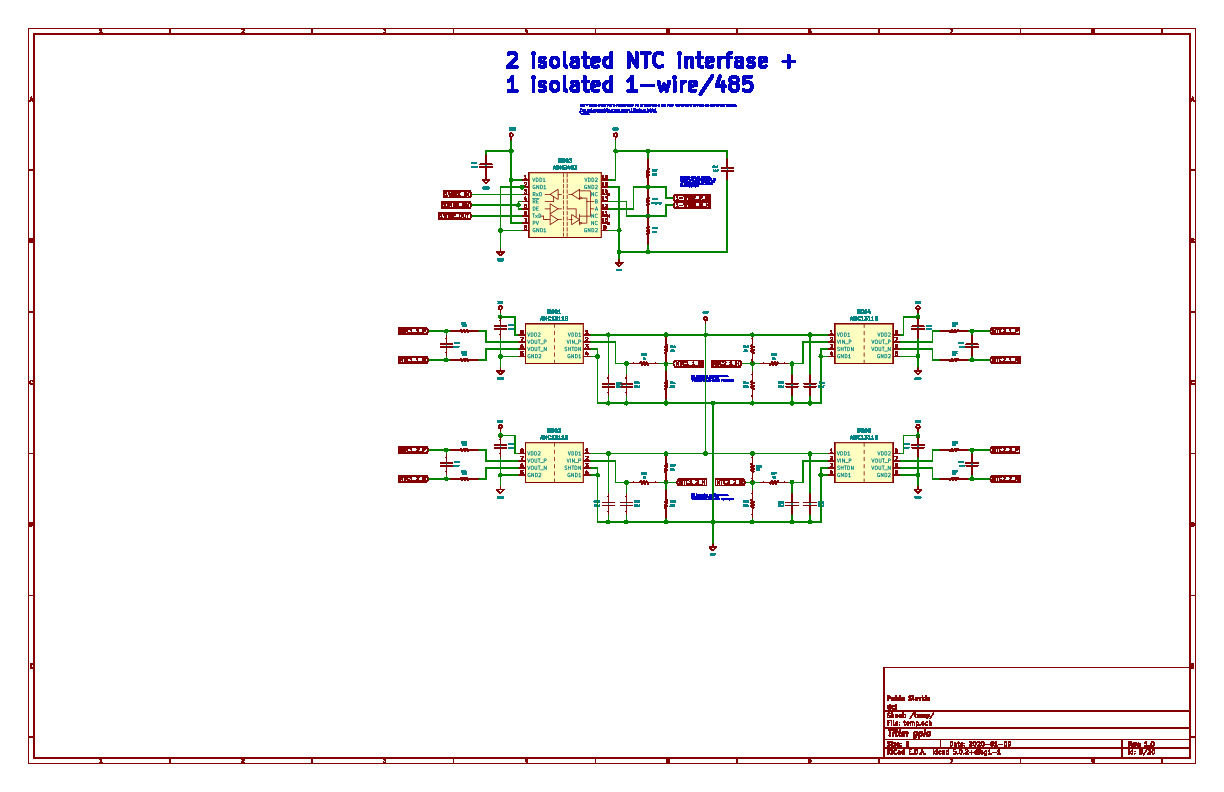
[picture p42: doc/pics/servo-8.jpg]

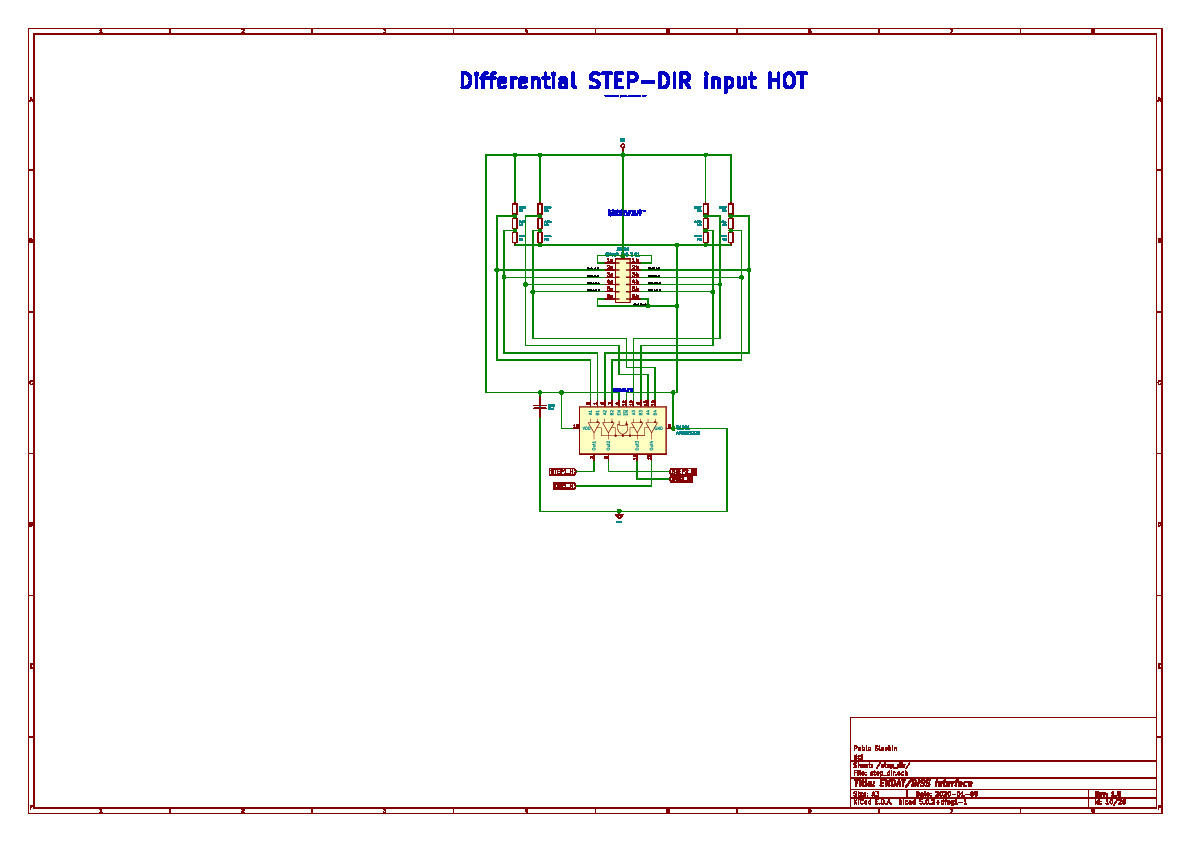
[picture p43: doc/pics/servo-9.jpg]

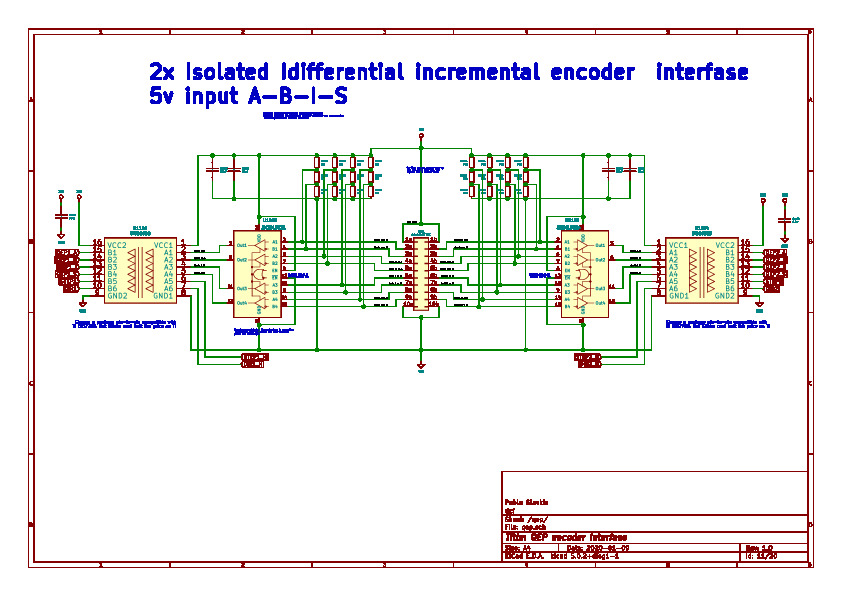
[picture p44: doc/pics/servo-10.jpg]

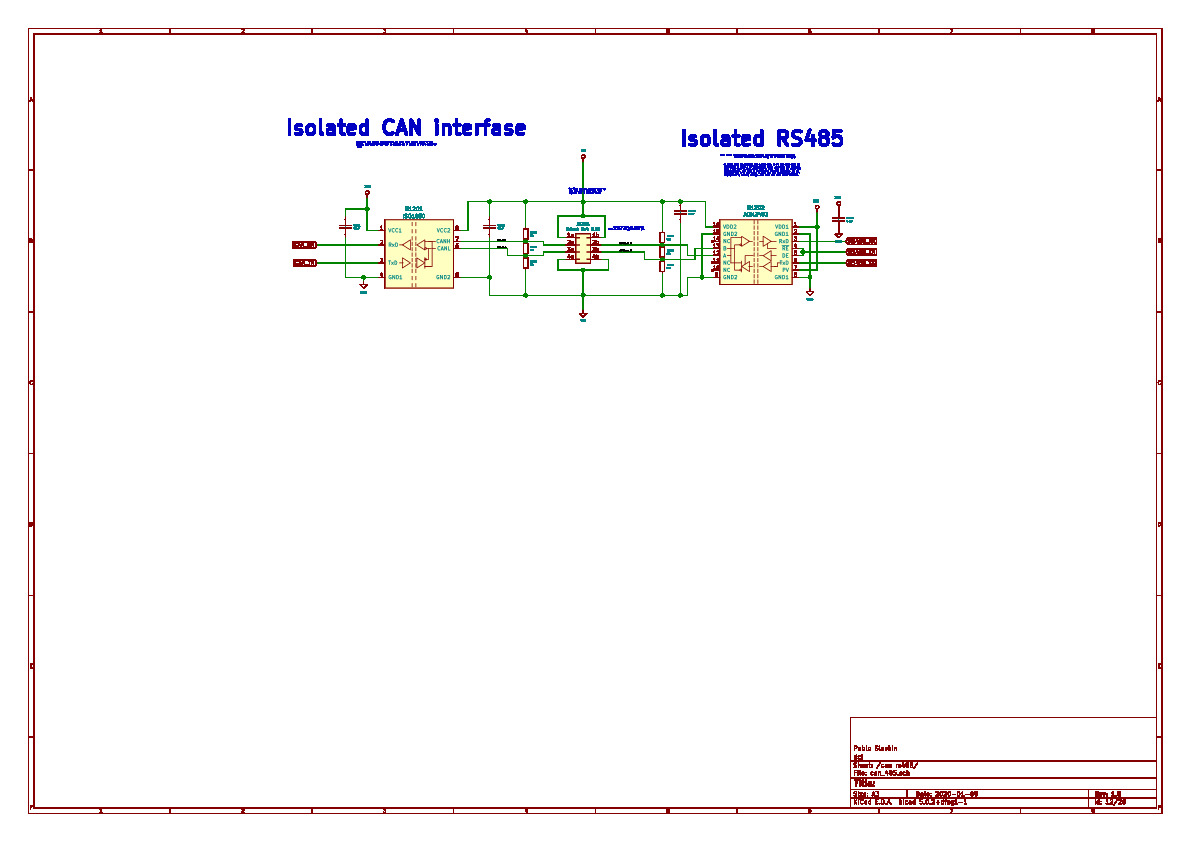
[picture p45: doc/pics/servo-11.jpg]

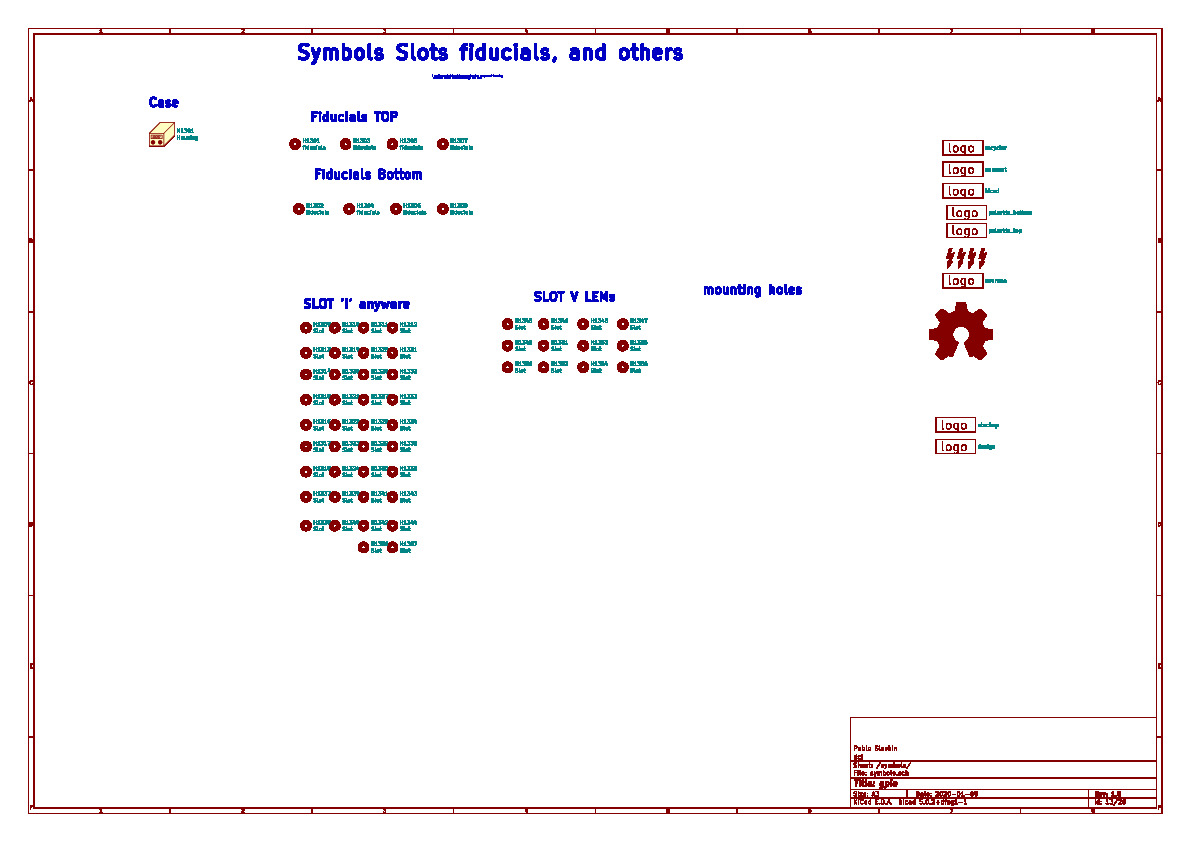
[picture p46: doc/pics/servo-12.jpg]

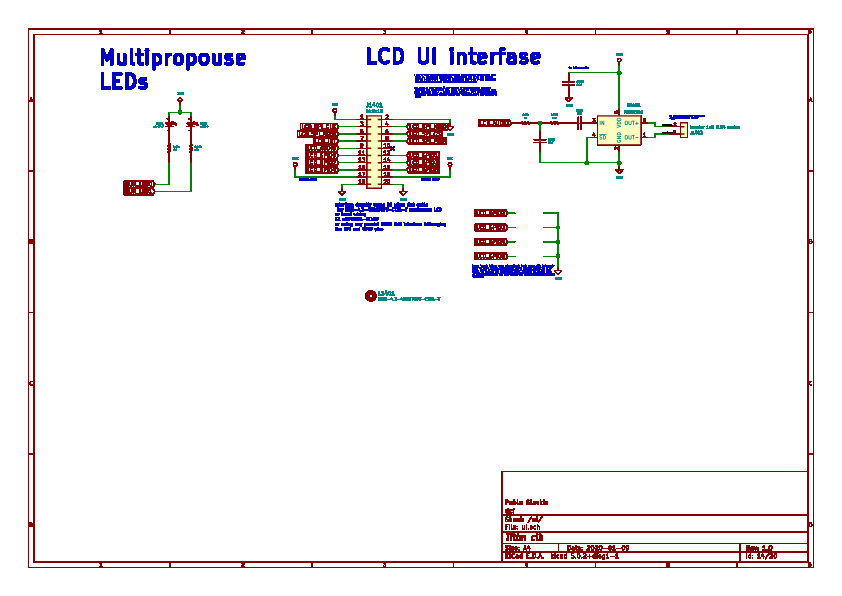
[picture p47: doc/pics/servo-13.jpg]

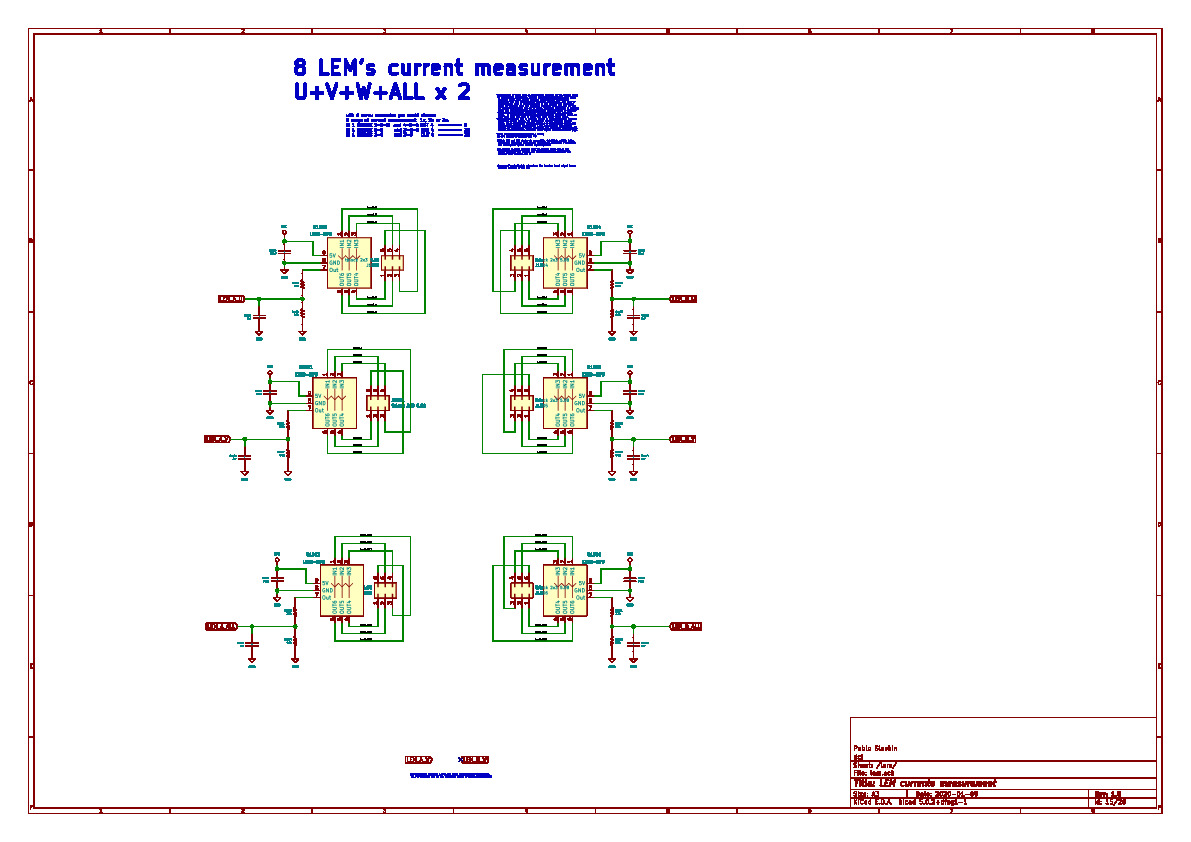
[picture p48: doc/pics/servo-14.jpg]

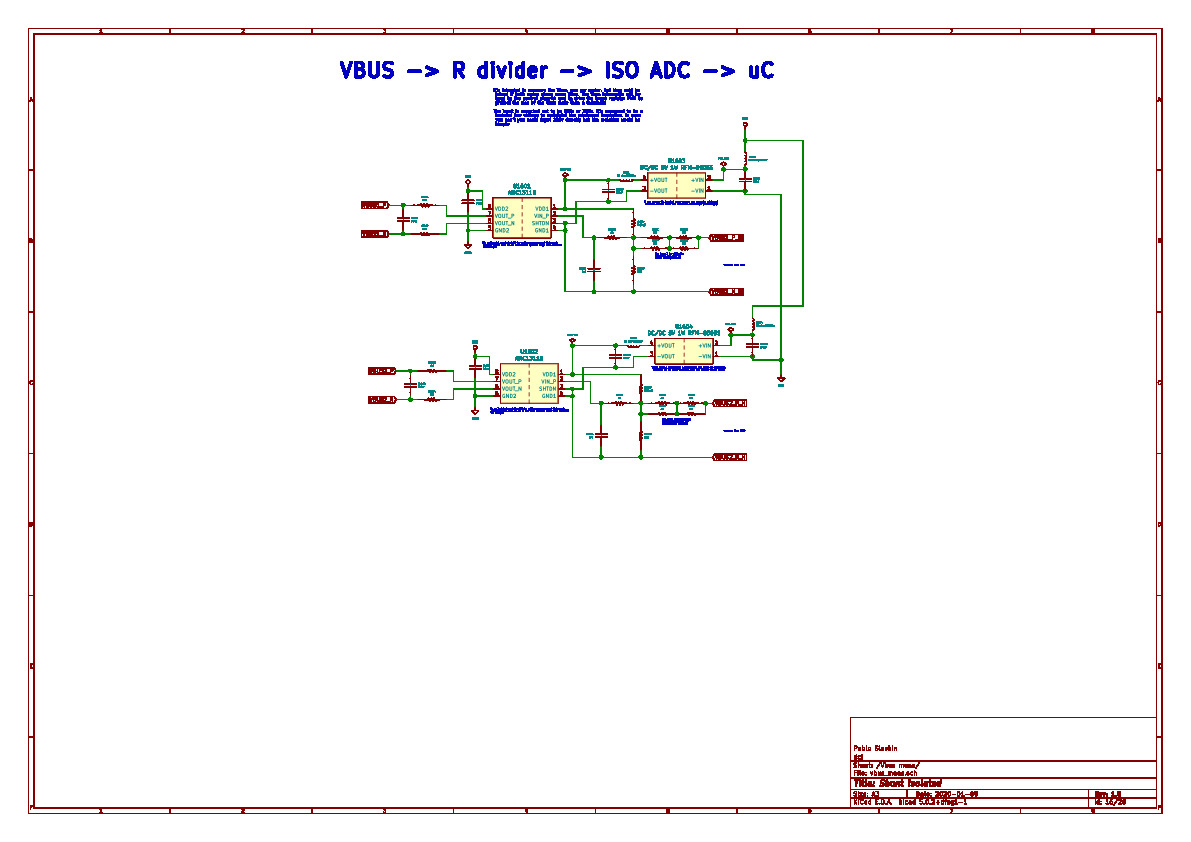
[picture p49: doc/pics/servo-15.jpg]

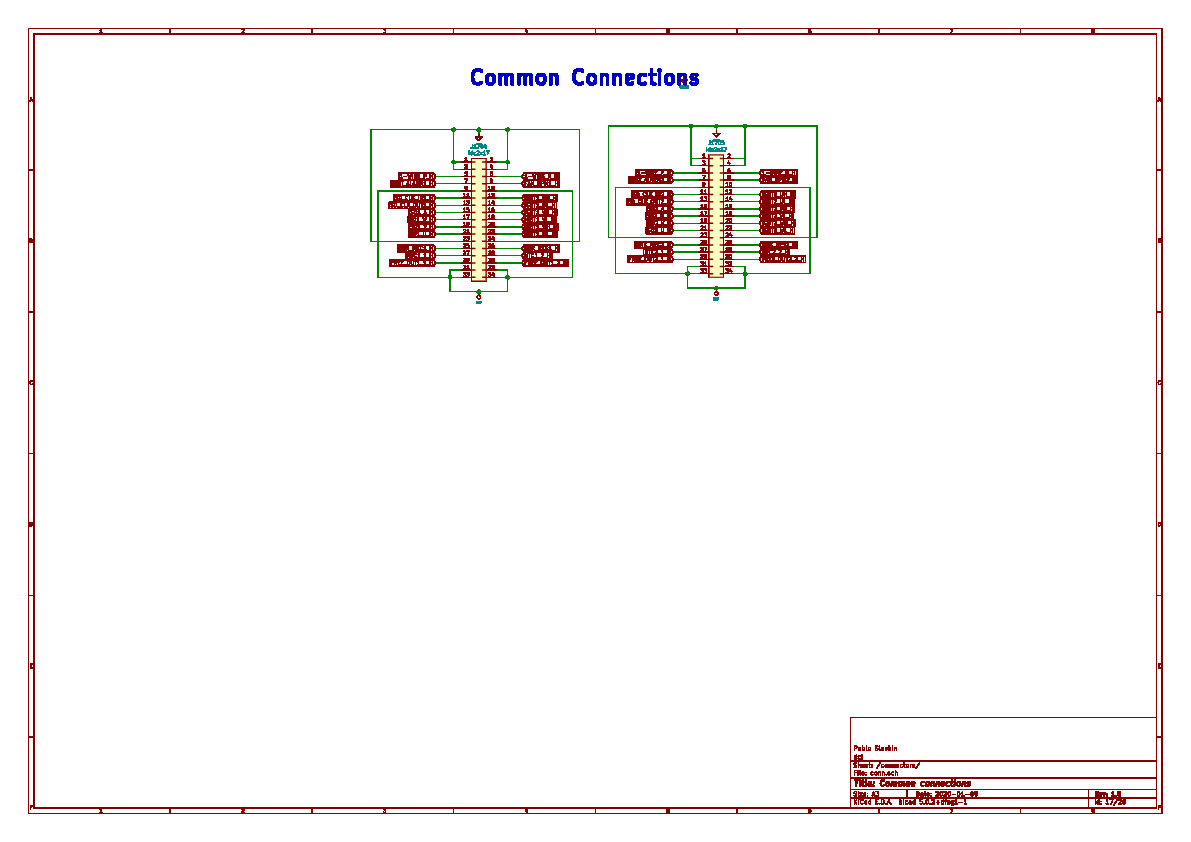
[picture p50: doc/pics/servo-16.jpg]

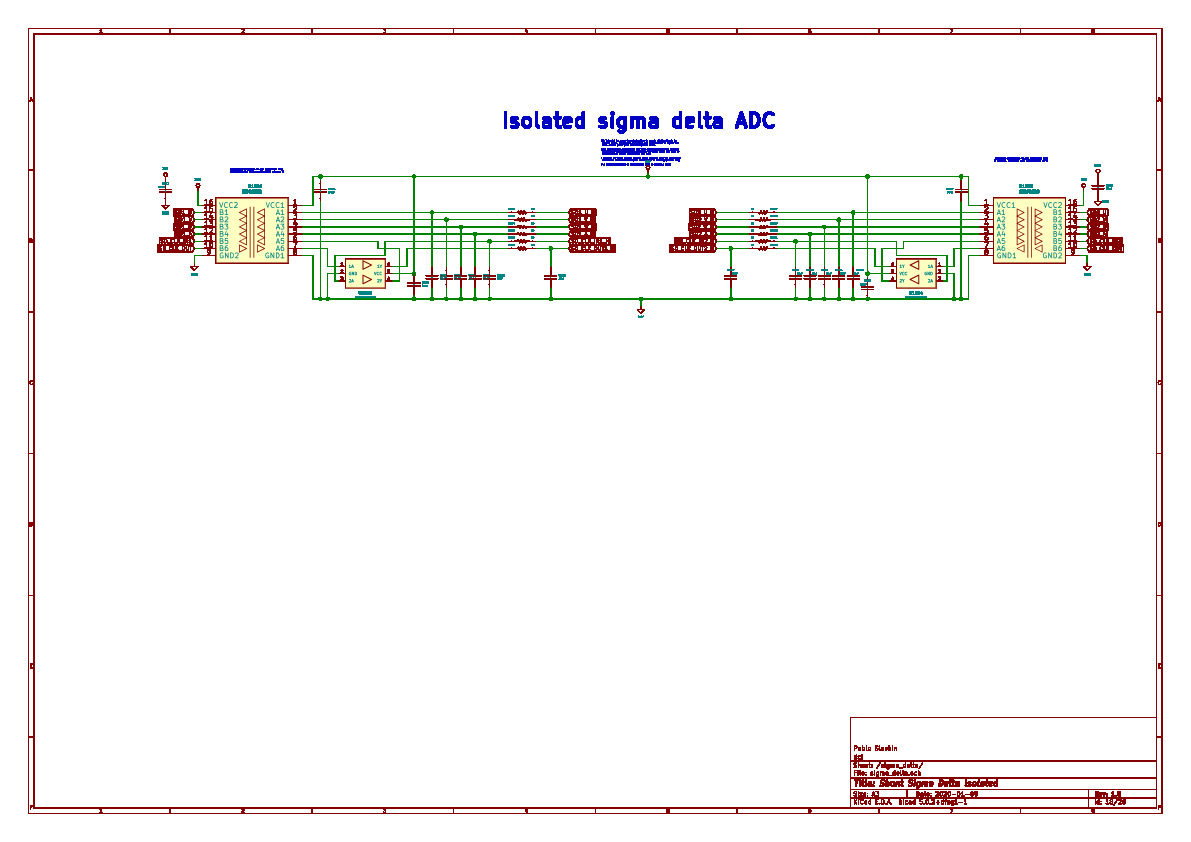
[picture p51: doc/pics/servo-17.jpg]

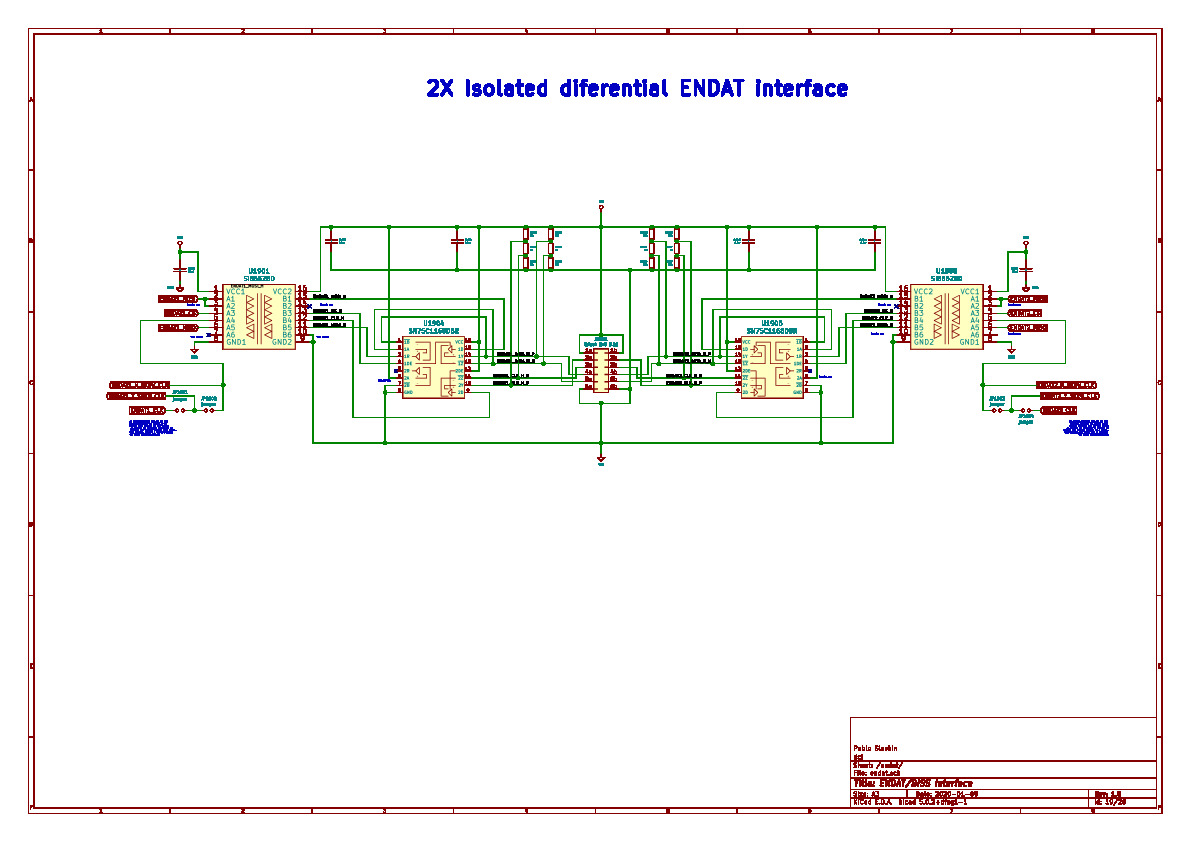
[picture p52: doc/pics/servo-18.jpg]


## Hierarchy

<!-- tree --ignore-case -L 3 -I "*utils*|*user*|*target*|*Debug*|Release|include|driverlib|tags|*types_c*" -->

```ruby

```

<!--

## Features
## Usage (Optional)
## Documentation (Optional)
## Tests (Optional)

- Going into more detail on code and technologies used
- I utilized this nifty <a href="https://github.com/adam-p/markdown-here/wiki/Markdown-Cheatsheet" target="_blank">Markdown Cheatsheet</a> for this sample `README`.

## Contributing

## Team

| <a href="https://github.com/pslavkin" target="_blank">**pslavkin**</a> | <a href="https://github.com/pslavkin" target="_blank">**neo**</a> | <a href="https://github.com/pslavkin" target="_blank">**doe**</a> |
| :---: |:---:| :---:|
| [![pslavkin](https://avatars1.githubusercontent.com/u/8507601?s=150)](https://github.com/pslavkin) | [<img src=https://media.metrolatam.com/2019/04/04/matrixreloadedneo01-3ec18ba895c91e664865ece4b3c9381d-600x400.jpg width="200" height="150">](https://github.com/pslavkin) | [<img src="https://encrypted-tbn0.gstatic.com/images?q=tbn:ANd9GcStNOGY8Cj2fH3B6L3OD91VJiuIq3iBA3FkCz0w0OJSQGuIxrsF" width="200" height="150">](https://github.com/pslavkin)  |
| <a href="https://github.com/pslavkin" target="_blank">`github.com/pslavkin`</a> | <a href="https://github.com/pslavkin" target="_blank">`github.com/pslavkin`</a> | <a href="https://github.com/pslavkin" target="_blank">`github.com/pslavkin`</a> |

## Support

Reach out to me at one of the following places!
- <a href="http://www.ti.com/tool/launchXL-F28379d#" target="_blank">**launchXL-F28379d** <img src="doc/pics/launchpad.jpeg"    title="launchpad"   width="100" height="100" alt="launchpad"></a>

## License

[![License](http://img.shields.io/:license-mit-blue.svg?style=flat-square)](http://badges.mit-license.org)

- **[MIT license](http://opensource.org/licenses/mit-license.php)**
- Copyright 2019 © <a href="http://fvcproductions.com" target="_blank">FVCproductions</a>.

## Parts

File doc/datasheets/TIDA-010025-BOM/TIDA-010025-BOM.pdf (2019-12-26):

010025E1(AMC1300-G1)_TI-BOM.xls | 010025
AMC1300-G1 | E1
10/10/2018 6:07:10 PM
TIDA-010025 | 010025 REV E1 Bill of Materials
Designator | Quantity | Value | PartNumber | Manufacturer | Description | PackageReference
!PCB1 | 1 | | 010025 | Any | Printed Circuit Board
C7 | 1 | 2uF | B32774D0205K000 | TDK | CAP, Film, 2 uF, 1100 V, +/- 10%, 0.011 ohm, TH | 31.5x21.5x12.5mm
C8, C10, C11, C13, C16, C18, C20, C22, C23, C25, C28, C30, C32, C34, C35, C37, C40, C42, C44, C46, C48, C54, C55, C58, C59, C62, C63, C70, C71, C78, C79, C81, C87, C91, C93, C95 | 36 | 0.1uF | GRM188R71H104KA93D | MuRata | CAP, CERM, 0.1 uF, 50 V, +/- 10%, X7R, 0603 | 0603
C9, C12, C17, C19, C21, C24, C29, C31, C33, C36, C41, C43, C45, C49, C92 | 15 | 4.7uF | GRM31CR71H475KA12L | MuRata | CAP, CERM, 4.7 uF, 50 V, +/- 10%, X7R, 1206 | 1206
C53, C56, C57, C60, C61, C64, C94 | 7 | 1uF | GRM21BR71C105KA01L | MuRata | CAP, CERM, 1 uF, 16 V, +/- 10%, X7R, 0805 | 0805
C65, C66, C67, C73 | 4 | 0.01uF | GRM188R71H103KA01D | MuRata | CAP, CERM, 0.01 uF, 50 V, +/- 10%, X7R, 0603 | 0603
D10, D11, D12 | 3 | 5.1V | BZX84C5V1-7-F | Diodes Inc. | Diode, Zener, 5.1 V, 300 mW, SOT-23 | SOT-23
H1, H2, H3, H4 | 4 | | NY PMS 440 0025 PH | B&F Fastener Supply | Machine Screw, Round, #4-40 x 1/4, Nylon, Philips panhead | Screw
H5, H6, H7, H8 | 4 | | 1902C | Keystone | Standoff, Hex, 0.5"L #4-40 Nylon | Standoff
J2, J4, J5, J6, J7 | 5 | | 1902547 | Phoenix Contact | Terminal Block, 9.52mm, 2x1, R/A, TH | Terminal Block, 2x1, Pitch 9.52mm
J23, J24, J25, J26 | 4 | | PEC03SAAN | Sullins Connector Solutions | Header, 100mil, 3x1, Tin, TH | Header, 3 PIN, 100mil, Tin
J27, J28 | 2 | | 5747846-4 | TE Connectivity | Receptacle, D-Sub, 25 Position, R/A, TH | Receptacle, D-Sub, 25 Position, R/A, TH
R1, R13 | 2 | 0.001 | ERJ-M1WTF1M0U | Panasonic | RES, 0.001, 1%, 1 W, 2512 | 2512
R2, R5, R7, R8, R9 | 5 | 200k | RC1206FR-07200KL | Yageo America | RES, 200 k, 1%, 0.25 W, 1206 | 1206
R3, R4, R6 | 3 | 0.01 | CSSH2728FT10L0 | Stackpole Electronics Inc | RES, 0.01, 1%, 4 W, AEC-Q200 Grade 0, 2728 | 2728
R10 | 1 | 22.0k | RC0603FR-0722KL | Yageo | RES, 22.0 k, 1%, 0.1 W, 0603 | 0603
R12 | 1 | 2.49k | RC1206FR-072K49L | Yageo America | RES, 2.49 k, 1%, 0.25 W, 1206 | 1206
R14, R15, R32, R33, R52, R53, R73, R74, R82, R86, R88, R90, R118, R119, R120, R123, R124, R125, R126, R127, R128 | 21 | 0 | RC0603JR-070RL | Yageo | RES, 0, 5%, 0.1 W, 0603 | 0603

Designator | Quantity | Value | PartNumber | Manufacturer | Description | PackageReference
R20, R21, R34, R35, R40, R41, R54, R55, R61, R62, R75, R76, R79, R83 | 14 | 120 | RC0603FR-07120RL | Yageo | RES, 120, 1%, 0.1 W, 0603 | 0603
R28, R29, R48, R49, R69, R70, R80 | 7 | 30.0 | RC1206FR-0730RL | Yageo America | RES, 30.0, 1%, 0.25 W, 1206 | 1206
R30, R31, R50, R51, R71, R72, R81 | 7 | 10.0k | RC0603FR-0710KL | Yageo | RES, 10.0 k, 1%, 0.1 W, 0603 | 0603
R85, R87, R89 | 3 | 806 | RC1206FR-07806RL | Yageo America | RES, 806, 1%, 0.25 W, 1206 | 1206
R91, R92, R93, R94, R95, R96 | 6 | 10.0 | RC0603FR-0710RL | Yageo | RES, 10.0, 1%, 0.1 W, 0603 | 0603
R101 | 1 | 100 | RC0603FR-07100RL | Yageo | RES, 100, 1%, 0.1 W, 0603 | 0603
R109 | 1 | 1.00k | RC0603FR-071KL | Yageo | RES, 1.00 k, 1%, 0.1 W, 0603 | 0603
R115 | 1 | 0 | RC1206JR-070RL | Yageo America | RES, 0, 5%, 0.25 W, 1206 | 1206
TP1, TP2, TP3, TP4, TP5, TP6, TP7, TP8, TP9, TP12, TP13, TP14, TP15, TP20, TP21, TP22, TP23, TP26, TP27, TP28, TP29, TP33, TP34, TP36, TP37, TP38, TP44, TP45, TP50, TP51, TP53, TP54, TP55, TP56, TP57, TP60, TP61 | 37 | | 5000 | Keystone | Test Point, Miniature, Red, TH | Red Miniature Testpoint
TP10, TP11, TP16, TP17, TP18, TP19, TP24, TP25, TP30, TP31, TP32, TP35, TP39, TP40, TP41, TP47, TP52, TP62, TP63 | 19 | | 5001 | Keystone | Test Point, Miniature, Black, TH | Black Miniature Testpoint
U1 | 1 | | 7MBR25VA120-50 | Fuji Electric | IGBT Module 1200V 25A, TH | 107.5x45mm
U2, U3, U4, U5, U6, U7, U8 | 7 | | UCC23513DWYR | Texas Instruments | 5-kVRMS, 3-A Single Channel Isolated Gate Driver with Opto Compatible Input, DWY0006A (SOIC-6) | DWY0006A
U12, U13, U14 | 3 | | AMC1300BDWVR | Texas Instruments | Precision Reinforced Isolated Amplifier for Current Sensing, DWV0008A (SOIC-8) | DWV0008A
U17, U20 | 2 | | AMC1311DWVR | Texas Instruments | Precision, 2-V Input, Reinforced Isolated Amplifier, DWV0008A (SOIC-8) | DWV0008A
U21 | 1 | | LP2951-50DR | Texas Instruments | Fixed Regulator with 1 to 30 V Input and 1.2 to 30 V Output, -40 to 125 degC, 8-Pin SOIC (D), Green (RoHS & no Sb/Br) | D0008A
C1, C2, C6 | 0 | 0.047uF | B32912A5473M000 | TDK | CAP, Film, 0.047 µF, 530 V,+/- 20%, TH | 18x8mm
C3, C4, C5 | 0 | 3300pF | B32021A3332M289 | TDK | CAP, Film, 3300 pF, 1500 V, +/- 20%, AEC-Q200 Grade 2, TH | 13x4x9mm

C14, C15, C26, C27, C38, C39, C47, C72, C75, C80, C83, C86, C88, C90, C108 | 0 | 0.01uF | GRM188R71H103KA01D | MuRata | CAP, CERM, 0.01 uF, 50 V, +/- 10%, X7R, 0603 | 0603
C50, C51, C52, C68, C69, C74, C76, C77, C82, C84, C85, C89, C97, C99, C101, C105, C107 | 0 | 0.1uF | GRM188R71H104KA93D | MuRata | CAP, CERM, 0.1 uF, 50 V, +/- 10%, X7R, 0603 | 0603
C96, C100 | 0 | 10uF | GRM21BZ71E106KE15L | MuRata | CAP, CERM, 10 uF, 25 V, +/- 10%, X7R, 0805 | 0805
C98 | 0 | 1uF | GRM21BR71C105KA01L | MuRata | CAP, CERM, 1 uF, 16 V, +/- 10%, X7R, 0805 | 0805
C102 | 0 | 1000pF | 202R18W102KV4E | Johanson Technology | CAP, CERM, 1000 pF, 2000 V, +/- 10%, X7R, 1206_190 | 1206_190
C103, C104, C106 | 0 | 4.7uF | GRM31CR71H475KA12L | MuRata | CAP, CERM, 4.7 uF, 50 V, +/- 10%, X7R, 1206 | 1206
D1, D2, D7 | 0 | 1200V | STTH112A | STMicroelectronics | Diode, Ultrafast, 1200 V, 1 A, SMA | SMA
D3, D4, D5, D6, D8, D9 | 0 | 30V | B130LAW-7-F | Diodes Inc. | Diode, Schottky, 30 V, 1 A, SOD-123 | SOD-123
D13, D14 | 0 | 20V | MBR0520LT1G | ON Semiconductor | Diode, Schottky, 20 V, 0.5 A, SOD-123 | SOD-123
J1, J3 | 0 | | 1902547 | Phoenix Contact | Terminal Block, 9.52mm, 2x1, R/A, TH | Terminal Block, 2x1, Pitch 9.52mm
J8, J9, J10, J11, J12, J13 | 0 | | 15912120 | Molex | Header, 100mil, 6x2, SMT | Header, 6x2, SMT
J22 | 0 | | PEC08SAAN | Sullins Connector Solutions | Header, 100mil, 8x1, Tin, TH | Header, 8x1, 100mil, TH
J29, J30 | 0 | | 282834-2 | TE Connectivity | Terminal Block, 2x1, 2.54mm, TH | Terminal Block, 2x1, 2.54mm, TH
Q1, Q2, Q3, Q4, Q5, Q6 | 0 | 30 V | BC848CLT1G | ON Semiconductor | Transistor, NPN, 30 V, 0.1 A, SOT-23 | SOT-23
R11, R36, R37, R56, R57, R77, R78, R84, R105, R114, R121, R122, R129, R130, R131, R132, R133, R134, R135, R136, R137, R138, R139 | 0 | 0 | RC0603JR-070RL | Yageo | RES, 0, 5%, 0.1 W, 0603 | 0603
R16, R17, R58 | 0 | 1.00 | RC1206FR-071RL | Yageo America | RES, 1.00, 1%, 0.25 W, 1206 | 1206
R18, R19, R38, R39, R59, R60 | 0 | 120 | RC0603FR-07120RL | Yageo | RES, 120, 1%, 0.1 W, 0603 | 0603
R22, R23, R42, R43, R63, R64, R116 | 0 | 0 | RC1206JR-070RL | Yageo America | RES, 0, 5%, 0.25 W, 1206 | 1206
R24, R26, R44, R46, R65, R67 | 0 | 3.01k | RC0603FR-073K01L | Yageo | RES, 3.01 k, 1%, 0.1 W, 0603 | 0603
R25, R27, R45, R47, R66, R68 | 0 | 20.0k | RC0603FR-0720KL | Yageo | RES, 20.0 k, 1%, 0.1 W, 0603 | 0603
R97, R99, R103, R104, R106, R108, R112, R113 | 0 | 10.0k | RC0603FR-0710KL | Yageo | RES, 10.0 k, 1%, 0.1 W, 0603 | 0603
R98, R100, R107, R110 | 0 | 10.0 | RC0603FR-0710RL | Yageo | RES, 10.0, 1%, 0.1 W, 0603 | 0603

R102, R111 | 0 | 15.0k | RC0603FR-0715KL | Yageo | RES, 15.0 k, 1%, 0.1 W, 0603 | 0603
R117 | 0 | 2.00Meg | RC1206FR-072ML | Yageo America | RES, 2.00 M, 1%, 0.25 W, 1206 | 1206
T1 | 0 | 475uH | 760390014 | Wurth Elektronik | Transformer, 475uH, SMT | 10.05x4.19x6.73 mm
TP42, TP43, TP48, TP49, TP58, TP59 | 0 | | 5000 | Keystone | Test Point, Miniature, Red, TH | Red Miniature Testpoint
TP46 | 0 | | 5001 | Keystone | Test Point, Miniature, Black, TH | Black Miniature Testpoint
U9, U10, U11, U22 | 0 | | TLV76050DBZR | Texas Instruments | 100-mA, 30-V, Fixed-Output, Linear-Voltage Regulator, DBZ0003A (SOT-23-3) | DBZ0003A
U15, U18 | 0 | | INA381A3DSG | Texas Instruments | 26-V, Low Cost, Zero-Drift, Voltage-Output, Current-Shunt Monitor With Integrated Comparator, DSG0008A (WSON-8) | DSG0008A
U16, U19 | 0 | | ISO7710DR | Texas Instruments | High Speed, Robust EMC Dual-Channel Digital Isolator, D0008B (SOIC-8) | D0008B
U23 | 0 | | SN6501DBVR | Texas Instruments | Low-Noise 350 mA, 410 kHz Transformer Driver, DBV0005A (SOT-23-5) | DBV0005A

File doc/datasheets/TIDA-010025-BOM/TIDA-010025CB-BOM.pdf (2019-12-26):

Filename: 010025CBE1(Buffer anode)_TI-BOM.xls | 010025CB
Variant: | Buffer anode | E1
Generated: 10/10/2018 5:39:12 PM
TID #: | TIDA-010025CB | 010025CB REV E1 Bill of Materials
Item # | Designator | Quantity | Value | PartNumber | Manufacturer | Description | PackageReference
1 | !PCB1 | 1 | | 010025CB | Any | Printed Circuit Board
2 | C1, C5, C15 | 3 | 680pF | GRM188R71H681KA01D | MuRata | CAP, CERM, 680 pF, 50 V, +/- 10%, X7R, 0603 | 0603
3 | C2, C13, C17, C18, C20, C22, C24, C27, C29, C31, C33, C39, C41, C42, C44, C46, C61, C62, C63 | 19 | 0.1uF | GRM188R71H104KA93D | MuRata | CAP, CERM, 0.1 uF, 50 V, +/- 10%, X7R, 0603 | 0603
4 | C3, C7, C8, C10, C12, C16 | 6 | 330pF | GRM188R71H331KA01D | MuRata | CAP, CERM, 330 pF, 50 V, +/- 10%, X7R, 0603 | 0603
5 | C4, C9, C14 | 3 | 2000pF | GRM1885C1H202JA01D | MuRata | CAP, CERM, 2000 pF, 50 V, +/- 5%, C0G/NP0, 0603 | 0603
6 | C6, C19, C21 | 3 | 0.01uF | GRM188R71H103KA01D | MuRata | CAP, CERM, 0.01 uF, 50 V, +/- 10%, X7R, 0603 | 0603
7 | C11 | 1 | 0.068uF | GRM188R71H683KA93D | MuRata | CAP, CERM, 0.068 uF, 50 V, +/- 10%, X7R, 0603 | 0603
8 | C23, C32, C45, C60 | 4 | 4.7uF | GRM31CR71H475KA12L | MuRata | CAP, CERM, 4.7 uF, 50 V, +/- 10%, X7R, 1206 | 1206
9 | C28, C30, C40, C43 | 4 | 1uF | GRM21BR71C105KA01L | MuRata | CAP, CERM, 1 uF, 16 V, +/- 10%, X7R, 0805 | 0805
10 | C34, C47 | 2 | 6800pF | GRM188R71H682KA01D | MuRata | CAP, CERM, 6800 pF, 50 V, +/- 10%, X7R, 0603 | 0603
11 | C35, C36, C48, C49 | 4 | 47uF | GRM32ER71A476ME15L | MuRata | CAP, CERM, 47 uF, 10 V, +/- 20%, X7R, 1210 | 1210
12 | C37, C50 | 2 | 5600pF | GRM188R71H562KA01D | MuRata | CAP, CERM, 5600 pF, 50 V, +/- 10%, X7R, 0603 | 0603
13 | C38, C51, C52 | 3 | 6.8pF | GRM1555C1H6R8CA01D | MuRata | CAP, CERM, 6.8 pF, 50 V, +/- 5%, C0G/NP0, 0402 | 0402
14 | C53, C54, C55, C56, C57, C58, C59 | 7 | 10pF | GRM1885C1H100JA01D | MuRata | CAP, CERM, 10 pF, 50 V, +/- 5%, C0G/NP0, 0603 | 0603
15 | D1 | 1 | 40V | SS24FL | Fairchild Semiconductor | Diode, Schottky, 40 V, 2 A, AEC-Q101, SOD-123F | SOD-123F
16 | D2 | 1 | 40V | SS14FL | Fairchild Semiconductor | Diode, Schottky, 40 V, 1 A, AEC-Q101, SOD-123F | SOD-123F
17 | FID1, FID2, FID3, FID4, FID5, FID6 | 6 | | N/A | N/A | Fiducial mark. There is nothing to buy or mount. | N/A
18 | H1, H2, H3, H4 | 4 | | NY PMS 440 0025 PH | B&F Fastener Supply | Machine Screw, Round, #4-40 x 1/4, Nylon, Philips panhead | Screw
19 | H5, H6, H7, H8 | 4 | | 1902C | Keystone | Standoff, Hex, 0.5"L #4-40 Nylon | Standoff
20 | J1, J2, J3, J4 | 4 | | PRPC010DAAN-RC | Sullins Connector Solutions | Header, 2.54mm, 10x2, Gold, TH | Header, 2.54mm, 10x2, TH
21 | J5 | 1 | | 282834-2 | TE Connectivity | Terminal Block, 2x1, 2.54mm, TH | Terminal Block, 2x1, 2.54mm, TH
22 | J6, J7 | 2 | | 5747846-4 | TE Connectivity | Receptacle, D-Sub, 25 Position, R/A, TH | Receptacle, D-Sub, 25 Position, R/A, TH
23 | L1 | 1 | 39uH | SDR1307-390KL | Bourns | Inductor, Drum Core, Ferrite, 39 uH, 2.9 A, 0.075 ohm, SMD | SDR1307
24 | L2 | 1 | 200uH | SDR1105-201KL | Bourns | Inductor, Drum Core, Ferrite, 200 uH, 1 A, 0.65 ohm, SMD | Inductor, 11.1x4.8x10mm
25 | R1, R49, R50, R54, R55, R115, R119, R120, R200 | 9 | 10.0k | RC0603FR-0710KL | Yageo | RES, 10.0 k, 1%, 0.1 W, 0603 | 0603
26 | R2, R9, R21, R30 | 4 | 1.5k | RC0603JR-071K5L | Yageo | RES, 1.5 k, 5%, 0.1 W, 0603 | 0603
27 | R3, R6, R8, R11, R16, R18, R23, R24, R26, R27, R29, R37, R66, R70, R71, R84, R85, R86, R87 | 19 | 1.00k | RC0603FR-071KL | Yageo | RES, 1.00 k, 1%, 0.1 W, 0603 | 0603
28 | R4, R10, R17, R28, R36 | 5 | 100 | RC0603FR-07100RL | Yageo | RES, 100, 1%, 0.1 W, 0603 | 0603

Item # | Designator | Quantity | Value | PartNumber | Manufacturer | Description | PackageReference
29 | R5, R13, R15, R19, R22, R31 | 6 | 681 | RC0603FR-07681RL | Yageo | RES, 681, 1%, 0.1 W, 0603 | 0603
30 | R7, R20, R33 | 3 | 866 | RC0603FR-07866RL | Yageo | RES, 866, 1%, 0.1 W, 0603 | 0603
31 | R12, R25, R35 | 3 | 4.99k | RC0603FR-074K99L | Yageo | RES, 4.99 k, 1%, 0.1 W, 0603 | 0603
32 | R14, R32, R39 | 3 | 294 | RC0603FR-07294RL | Yageo | RES, 294, 1%, 0.1 W, 0603 | 0603
33 | R34, R59, R60, R61, R62, R72, R73, R74, R92, R93, R94, R104, R105, R106, R114, R116 | 16 | 0 | RC0603JR-070RL | Yageo | RES, 0, 5%, 0.1 W, 0603 | 0603
34 | R38 | 1 | 2.08k | RT0603BRD072K08L | Yageo America | RES, 2.08 k, 0.1%, 0.1 W, 0603 | 0603
35 | R40 | 1 | 10.0k | RT0603BRD0710KL | Yageo America | RES, 10.0 k, 0.1%, 0.1 W, 0603 | 0603
36 | R42 | 1 | 0 | RC1206JR-070RL | Yageo America | RES, 0, 5%, 0.25 W, 1206 | 1206
37 | R44 | 1 | 100k | RC0603FR-07100KL | Yageo | RES, 100 k, 1%, 0.1 W, 0603 | 0603
38 | R45 | 1 | 40.2k | RC0603FR-0740K2L | Yageo | RES, 40.2 k, 1%, 0.1 W, 0603 | 0603
39 | R46, R52 | 2 | 287k | RC0603FR-07287KL | Yageo | RES, 287 k, 1%, 0.1 W, 0603 | 0603
40 | R47 | 1 | 6.65k | RC0603FR-076K65L | Yageo | RES, 6.65 k, 1%, 0.1 W, 0603 | 0603
41 | R48 | 1 | 56.2k | RC0603FR-0756K2L | Yageo | RES, 56.2 k, 1%, 0.1 W, 0603 | 0603
42 | R51 | 1 | 71.5k | RC0603FR-0771K5L | Yageo | RES, 71.5 k, 1%, 0.1 W, 0603 | 0603
43 | R53 | 1 | 133k | RC0603FR-07133KL | Yageo | RES, 133 k, 1%, 0.1 W, 0603 | 0603
44 | TP2, TP7, TP8, TP9, TP10, TP11, TP17, TP18, TP20, TP21, TP22, TP30, TP31 | 13 | | 5000 | Keystone | Test Point, Miniature, Red, TH | Red Miniature Testpoint
45 | TP23, TP24 | 2 | | 5001 | Keystone | Test Point, Miniature, Black, TH | Black Miniature Testpoint
46 | U1, U4 | 2 | | LMV339MT/NOPB | Texas Instruments | Quad General Purpose, Low Voltage, Tiny Pack Comparator, 14-pin TSSOP, Pb-Free | PW0014A
47 | U2 | 1 | | TLV9064IDR | Texas Instruments | 4 channel, 10-MHz, Low-Noise, RRIO, CMOS Operational Amplifier for Cost-Sensitive Systems, D0014A (SOIC-14) | D0014A
48 | U3 | 1 | | TLV9002IDR | Texas Instruments | 2-Channel, 1MHz, RRIO, 1.8V to 5.5V Operational Amplifier for Cost-Optimized Systems, D0008A (SOIC-8) | D0008A
49 | U5 | 1 | | TLV431AIDBVR | Texas Instruments | Low Voltage Adjustable Precision Shunt Regulator, 39 ppm / degC, 15 mA, -40 to 85 degC, 5-pin SOT-23 (DBV), Green (RoHS & no Sb/Br) | DBV0005A
50 | U6, U8 | 2 | | TPS54140ADRCR | Texas Instruments | 3.5V to 42V Input, 1.5A Step-Down Converter with Eco-Mode, DRC0010J (VSON-10) | DRC0010J
51 | U7 | 1 | | TLV1117LV33DCYR | Texas Instruments | Single Output LDO, 1 A, Fixed 3.3 V Output, 2 to 5.5 V Input, 4-pin SOT-223 (DCY), -40 to 125 degC, Green (RoHS & no Sb/Br) | DCY0004A
52 | U9 | 1 | | TLV1117-50IDCY | Texas Instruments | Single-Output LDO, 800mA, Fixed (5.0), Internal Current Limit, Thermal Overload Protection, DCY0004A (SOT-223-4) | DCY0004A
53 | U10 | 1 | | SN74LVC1G10DCKR | Texas Instruments | Single 3-Input Positive-NAND Gate, DCK0006A (SOT-SC70-6) | DCK0006A
54 | U11 | 1 | | SN74ACT244DWR | Texas Instruments | Octal Buffers/Drivers With 3-State Outputs, DW0020A, LARGE T&R | DW0020A
55 | U12 | 1 | | SN74LVC1G32DCKR | Texas Instruments | Single 2-Input Positive-OR Gate, DCK0005A, LARGE T&R | DCK0005A
56 | C25 | 0 | 1000pF | 202R18W102KV4E | Johanson Technology | CAP, CERM, 1000 pF, 2000 V, +/- 10%, X7R, 1206_190 | 1206_190
57 | C26 | 0 | 4.7uF | GRM31CR71H475KA12L | MuRata | CAP, CERM, 4.7 uF, 50 V, +/- 10%, X7R, 1206 | 1206
58 | Q1, Q2, Q3, Q4, Q5, Q6, Q7 | 0 | 30V | CSD17571Q2 | Texas Instruments | MOSFET, N-CH, 30 V, 22 A, DQK0006C (WSON-6) | DQK0006C
59 | R41 | 0 | 0 | RC1206JR-070RL | Yageo America | RES, 0, 5%, 0.25 W, 1206 | 1206
60 | R43 | 0 | 2.00Meg | RC1206FR-072ML | Yageo America | RES, 2.00 M, 1%, 0.25 W, 1206 | 1206

Item # | Designator | Quantity | Value | PartNumber | Manufacturer | Description | PackageReference
61 | R56, R57, R58, R63, R64, R65, R67, R68, R69, R81, R82, R83, R88, R89, R90, R91, R95, R96, R97, R98, R99, R100, R101, R102, R103, R113 | 0 | 0 | RC0603JR-070RL | Yageo | RES, 0, 5%, 0.1 W, 0603 | 0603
62 | R75, R76, R77, R107, R108, R109, R117 | 0 | 1.00k | RC0603FR-071KL | Yageo | RES, 1.00 k, 1%, 0.1 W, 0603 | 0603
63 | R78, R79, R80, R110, R111, R112, R118 | 0 | 10.0k | RC0603FR-0710KL | Yageo | RES, 10.0 k, 1%, 0.1 W, 0603 | 0603

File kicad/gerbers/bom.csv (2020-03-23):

Source: | /home/pslavkin/servo_pmsm_orphano/kicad/servo.sch
Date: | Mon 23 Mar 2020 02:42:34 AM -03
Tool: | Eeschema 5.0.2+dfsg1-1
Generator: | /usr/share/kicad/plugins/bom_csv_grouped_by_value.py
Component Count: | 609
Individual Components:
Item | Qty | Reference(s) | Value | LibPart | Footprint | Datasheet | Description | Fieldname | PartNumber | bom_1 | bom_2 | bom_3 | digikey | price@10
 |  | C202 | 0.1uF | servo:Capacitor | servo:C_0603_1608Metric |  | CAP CER 0.1UF 16V X7R 0603 |  | CC0603KPX7R7BB104 | 1 | 1 | 1 | 311-1335-1-ND | 0.05800
 |  | C204 | 10uF | servo:Capacitor | servo:C_0603_1608Metric |  | 10µF ±20% 10V Ceramic Capacitor X5R 0603 (1608 Metric) |  | GRM188R61A106ME69D | 1 | 1 | 1 | 490-10475-1-ND | 0.15400
 |  | C205 | 10uF | servo:Capacitor | servo:C_0603_1608Metric |  | 10µF ±20% 10V Ceramic Capacitor X5R 0603 (1608 Metric) |  | GRM188R61A106ME69D | 1 | 1 | 1 | 490-10475-1-ND | 0.15400
 |  | C207 | 0.1uF | servo:Capacitor | servo:C_0603_1608Metric |  | CAP CER 0.1UF 16V X7R 0603 |  | CC0603KPX7R7BB104 | 1 | 1 | 1 | 311-1335-1-ND | 0.05800
 |  | C209 | 0.1uF | servo:Capacitor | servo:C_0603_1608Metric |  | CAP CER 0.1UF 16V X7R 0603 |  | CC0603KPX7R7BB104 | 1 | 1 | 1 | 311-1335-1-ND | 0.05800
 |  | C211 | 0.1uF | servo:Capacitor | servo:C_0603_1608Metric |  | CAP CER 0.1UF 16V X7R 0603 |  | CC0603KPX7R7BB104 | 1 | 1 | 1 | 311-1335-1-ND | 0.05800
 |  | C214 | 1uF | servo:Capacitor | servo:C_0603_1608Metric |  | CAP CER 1UF 10V X7R 0603 |  | C0603C105K8RACTU | 1 | 1 | 1 | 399-11133-1-ND | 0.06400
 |  | C216 | 1uF | servo:Capacitor | servo:C_0603_1608Metric |  | CAP CER 1UF 10V X7R 0603 |  | C0603C105K8RACTU | 1 | 1 | 1 | 399-11133-1-ND | 0.06400
 |  | C217 | 4n7 | servo:Capacitor | servo:C_1206_3216Metric |  | 4700pF ±10% 100V Ceramic Capacitor X7R 1206 (3216 Metric) |  | 12061C472KAT2A | 1 | 1 | 1 | 478-1521-1-ND | 0.18700
 |  | C301 | 10uF | servo:Capacitor | servo:C_0603_1608Metric |  | 10µF ±20% 10V Ceramic Capacitor X5R 0603 (1608 Metric) |  | GRM188R61A106ME69D | 1 | 1 | 1 | 490-10475-1-ND | 0.15400
 |  | C302 | 0.1uF | servo:Capacitor | servo:C_0603_1608Metric |  | CAP CER 0.1UF 16V X7R 0603 |  | CC0603KPX7R7BB104 | 1 | 1 | 1 | 311-1335-1-ND | 0.05800
 |  | C303 | 10uF | servo:Capacitor | servo:C_0603_1608Metric |  | 10µF ±20% 10V Ceramic Capacitor X5R 0603 (1608 Metric) |  | GRM188R61A106ME69D | 1 | 1 | 1 | 490-10475-1-ND | 0.15400
 |  | C304 | 0.1uF | servo:Capacitor | servo:C_0603_1608Metric |  | CAP CER 0.1UF 16V X7R 0603 |  | CC0603KPX7R7BB104 | 1 | 1 | 1 | 311-1335-1-ND | 0.05800
 |  | C404 | 0.1uF | servo:Capacitor | servo:C_0603_1608Metric |  | CAP CER 0.1UF 16V X7R 0603 |  | CC0603KPX7R7BB104 | 1 | 1 | 1 | 311-1335-1-ND | 0.05800
 |  | C405 | 0.1uF | servo:Capacitor | servo:C_0603_1608Metric |  | CAP CER 0.1UF 16V X7R 0603 |  | CC0603KPX7R7BB104 | 1 | 1 | 1 | 311-1335-1-ND | 0.05800
 |  | C407 | 10uF | servo:Capacitor | servo:C_0603_1608Metric |  | 10µF ±20% 10V Ceramic Capacitor X5R 0603 (1608 Metric) |  | GRM188R61A106ME69D | 1 | 1 | 1 | 490-10475-1-ND | 0.15400
 |  | C408 | 10uF | servo:Capacitor | servo:C_0603_1608Metric |  | 10µF ±20% 10V Ceramic Capacitor X5R 0603 (1608 Metric) |  | GRM188R61A106ME69D | 1 | 1 | 1 | 490-10475-1-ND | 0.15400
 |  | C409 | 10uF | servo:Capacitor | servo:C_0603_1608Metric |  | 10µF ±20% 10V Ceramic Capacitor X5R 0603 (1608 Metric) |  | GRM188R61A106ME69D | 1 | 1 | 1 | 490-10475-1-ND | 0.15400
 |  | C410 | 10uF | servo:Capacitor | servo:C_0603_1608Metric |  | 10µF ±20% 10V Ceramic Capacitor X5R 0603 (1608 Metric) |  | GRM188R61A106ME69D | 1 | 1 | 1 | 490-10475-1-ND | 0.15400
 |  | C411 | 0.1uF | servo:Capacitor | servo:C_0603_1608Metric |  | CAP CER 0.1UF 16V X7R 0603 |  | CC0603KPX7R7BB104 | 1 | 1 | 1 | 311-1335-1-ND | 0.05800
 |  | C412 | 0.1uF | servo:Capacitor | servo:C_0603_1608Metric |  | CAP CER 0.1UF 16V X7R 0603 |  | CC0603KPX7R7BB104 | 1 | 1 | 1 | 311-1335-1-ND | 0.05800
 |  | C414 | 0.1uF | servo:Capacitor | servo:C_0603_1608Metric |  | CAP CER 0.1UF 16V X7R 0603 |  | CC0603KPX7R7BB104 | 1 | 1 | 1 | 311-1335-1-ND | 0.05800
 |  | C418 | 0.1uF | servo:Capacitor | servo:C_0603_1608Metric |  | CAP CER 0.1UF 16V X7R 0603 |  | CC0603KPX7R7BB104 | 1 | 1 | 1 | 311-1335-1-ND | 0.05800
 |  | C419 | 0.1uF | servo:Capacitor | servo:C_0603_1608Metric |  | CAP CER 0.1UF 16V X7R 0603 |  | CC0603KPX7R7BB104 | 1 | 1 | 1 | 311-1335-1-ND | 0.05800
 |  | C422 | 0.1uF | servo:Capacitor | servo:C_0603_1608Metric |  | CAP CER 0.1UF 16V X7R 0603 |  | CC0603KPX7R7BB104 | 1 | 1 | 1 | 311-1335-1-ND | 0.05800
 |  | C423 | 0.1uF | servo:Capacitor | servo:C_0603_1608Metric |  | CAP CER 0.1UF 16V X7R 0603 |  | CC0603KPX7R7BB104 | 1 | 1 | 1 | 311-1335-1-ND | 0.05800
 |  | C426 | 1uF | servo:Capacitor | servo:C_0603_1608Metric |  | CAP CER 1UF 10V X7R 0603 |  | C0603C105K8RACTU | 1 | 1 | 1 | 399-11133-1-ND | 0.06400
 |  | C427 | 1uF | servo:Capacitor | servo:C_0603_1608Metric |  | CAP CER 1UF 10V X7R 0603 |  | C0603C105K8RACTU | 1 | 1 | 1 | 399-11133-1-ND | 0.06400
 |  | C428 | 1uF | servo:Capacitor | servo:C_0603_1608Metric |  | CAP CER 1UF 10V X7R 0603 |  | C0603C105K8RACTU | 1 | 1 | 1 | 399-11133-1-ND | 0.06400
 |  | C429 | 1uF | servo:Capacitor | servo:C_0603_1608Metric |  | CAP CER 1UF 10V X7R 0603 |  | C0603C105K8RACTU | 1 | 1 | 1 | 399-11133-1-ND | 0.06400
 |  | C434 | 4n7 | servo:Capacitor | servo:C_1206_3216Metric |  | 4700pF ±10% 100V Ceramic Capacitor X7R 1206 (3216 Metric) |  | 12061C472KAT2A | 1 | 1 | 1 | 478-1521-1-ND | 0.18700
 |  | C501 | 0.1uF | servo:Capacitor | servo:C_0603_1608Metric |  | CAP CER 0.1UF 16V X7R 0603 |  | CC0603KPX7R7BB104 | 1 | 1 | 1 | 311-1335-1-ND | 0.05800
 |  | C502 | 0.1uF | servo:Capacitor | servo:C_0603_1608Metric |  | CAP CER 0.1UF 16V X7R 0603 |  | CC0603KPX7R7BB104 | 1 | 1 | 1 | 311-1335-1-ND | 0.05800
 |  | C503 | 0.1uF | servo:Capacitor | servo:C_0603_1608Metric |  | CAP CER 0.1UF 16V X7R 0603 |  | CC0603KPX7R7BB104 | 1 | 1 | 1 | 311-1335-1-ND | 0.05800
 |  | C504 | 0.1uF | servo:Capacitor | servo:C_0603_1608Metric |  | CAP CER 0.1UF 16V X7R 0603 |  | CC0603KPX7R7BB104 | 1 | 1 | 1 | 311-1335-1-ND | 0.05800
 |  | C505 | 0.1uF | servo:Capacitor | servo:C_0603_1608Metric |  | CAP CER 0.1UF 16V X7R 0603 |  | CC0603KPX7R7BB104 | 1 | 1 | 1 | 311-1335-1-ND | 0.05800
 |  | C506 | 0.1uF | servo:Capacitor | servo:C_0603_1608Metric |  | CAP CER 0.1UF 16V X7R 0603 |  | CC0603KPX7R7BB104 | 1 | 1 | 1 | 311-1335-1-ND | 0.05800
 |  | C507 | 0.1uF | servo:Capacitor | servo:C_0603_1608Metric |  | CAP CER 0.1UF 16V X7R 0603 |  | CC0603KPX7R7BB104 | 1 | 1 | 1 | 311-1335-1-ND | 0.05800
 |  | C508 | 2.2uF | servo:Capacitor | servo:C_0603_1608Metric |  | CAP CER 2.2UF 16V X6S 0603 |  | GRT188C81C225KE13D | 1 | 1 | 1 | 490-12287-1-ND | 0.35500
 |  | C511 | 0.1uF | servo:Capacitor | servo:C_0603_1608Metric |  | CAP CER 0.1UF 16V X7R 0603 |  | CC0603KPX7R7BB104 | 1 | 1 | 1 | 311-1335-1-ND | 0.05800
 |  | C512 | 0.1uF | servo:Capacitor | servo:C_0603_1608Metric |  | CAP CER 0.1UF 16V X7R 0603 |  | CC0603KPX7R7BB104 | 1 | 1 | 1 | 311-1335-1-ND | 0.05800
 |  | C514 | 0.1uF | servo:Capacitor | servo:C_0603_1608Metric |  | CAP CER 0.1UF 16V X7R 0603 |  | CC0603KPX7R7BB104 | 1 | 1 | 1 | 311-1335-1-ND | 0.05800
 |  | C515 | 0.1uF | servo:Capacitor | servo:C_0603_1608Metric |  | CAP CER 0.1UF 16V X7R 0603 |  | CC0603KPX7R7BB104 | 1 | 1 | 1 | 311-1335-1-ND | 0.05800
 |  | C516 | 0.1uF | servo:Capacitor | servo:C_0603_1608Metric |  | CAP CER 0.1UF 16V X7R 0603 |  | CC0603KPX7R7BB104 | 1 | 1 | 1 | 311-1335-1-ND | 0.05800
 |  | C517 | 0.1uF | servo:Capacitor | servo:C_0603_1608Metric |  | CAP CER 0.1UF 16V X7R 0603 |  | CC0603KPX7R7BB104 | 1 | 1 | 1 | 311-1335-1-ND | 0.05800
 |  | C518 | 0.1uF | servo:Capacitor | servo:C_0603_1608Metric |  | CAP CER 0.1UF 16V X7R 0603 |  | CC0603KPX7R7BB104 | 1 | 1 | 1 | 311-1335-1-ND | 0.05800
 |  | C519 | 0.1uF | servo:Capacitor | servo:C_0603_1608Metric |  | CAP CER 0.1UF 16V X7R 0603 |  | CC0603KPX7R7BB104 | 1 | 1 | 1 | 311-1335-1-ND | 0.05800
 |  | C520 | 0.1uF | servo:Capacitor | servo:C_0603_1608Metric |  | CAP CER 0.1UF 16V X7R 0603 |  | CC0603KPX7R7BB104 | 1 | 1 | 1 | 311-1335-1-ND | 0.05800
 |  | C521 | 0.1uF | servo:Capacitor | servo:C_0603_1608Metric |  | CAP CER 0.1UF 16V X7R 0603 |  | CC0603KPX7R7BB104 | 1 | 1 | 1 | 311-1335-1-ND | 0.05800
 |  | C523 | 0.1uF | servo:Capacitor | servo:C_0603_1608Metric |  | CAP CER 0.1UF 16V X7R 0603 |  | CC0603KPX7R7BB104 | 1 | 1 | 1 | 311-1335-1-ND | 0.05800
 |  | C524 | 0.1uF | servo:Capacitor | servo:C_0603_1608Metric |  | CAP CER 0.1UF 16V X7R 0603 |  | CC0603KPX7R7BB104 | 1 | 1 | 1 | 311-1335-1-ND | 0.05800
 |  | C525 | 0.1uF | servo:Capacitor | servo:C_0603_1608Metric |  | CAP CER 0.1UF 16V X7R 0603 |  | CC0603KPX7R7BB104 | 1 | 1 | 1 | 311-1335-1-ND | 0.05800
 |  | C526 | 10uF | servo:Capacitor | servo:C_0603_1608Metric |  | 10µF ±20% 10V Ceramic Capacitor X5R 0603 (1608 Metric) |  | GRM188R61A106ME69D | 1 | 1 | 1 | 490-10475-1-ND | 0.15400
 |  | C529 | 2.2uF | servo:Capacitor | servo:C_0603_1608Metric |  | CAP CER 2.2UF 16V X6S 0603 |  | GRT188C81C225KE13D | 1 | 1 | 1 | 490-12287-1-ND | 0.35500
 |  | C530 | 10uF | servo:Capacitor | servo:C_0603_1608Metric |  | 10µF ±20% 10V Ceramic Capacitor X5R 0603 (1608 Metric) |  | GRM188R61A106ME69D | 1 | 1 | 1 | 490-10475-1-ND | 0.15400
 |  | C531 | 2.2uF | servo:Capacitor | servo:C_0603_1608Metric |  | CAP CER 2.2UF 16V X6S 0603 |  | GRT188C81C225KE13D | 1 | 1 | 1 | 490-12287-1-ND | 0.35500
 |  | C601 | 0.1uF | servo:Capacitor | servo:C_0603_1608Metric |  | CAP CER 0.1UF 16V X7R 0603 |  | CC0603KPX7R7BB104 | 1 | 1 | 1 | 311-1335-1-ND | 0.05800
 |  | C602 | 0.1uF | servo:Capacitor | servo:C_0603_1608Metric |  | CAP CER 0.1UF 16V X7R 0603 |  | CC0603KPX7R7BB104 | 1 | 1 | 1 | 311-1335-1-ND | 0.05800
 |  | C603 | 0.1uF | servo:Capacitor | servo:C_0603_1608Metric |  | CAP CER 0.1UF 16V X7R 0603 |  | CC0603KPX7R7BB104 | 1 | 1 | 1 | 311-1335-1-ND | 0.05800
 |  | C701 | 22uF | servo:Capacitor | servo:C_0603_1608Metric |  | CAP CER 22UF 6.3V X5R 0603 |  | GRM188R60J226MEA0D | 1 | 1 | 1 | 490-7611-1-ND | 0.19400
 |  | C702 | 2.2uF | servo:Capacitor | servo:C_0603_1608Metric |  | CAP CER 2.2UF 16V X6S 0603 |  | GRT188C81C225KE13D | 1 | 1 | 1 | 490-12287-1-ND | 0.35500
 |  | C703 | 0.1uF | servo:Capacitor | servo:C_0603_1608Metric |  | CAP CER 0.1UF 16V X7R 0603 |  | CC0603KPX7R7BB104 | 1 | 1 | 1 | 311-1335-1-ND | 0.05800
 |  | C704 | 22uF | servo:Capacitor | servo:C_0603_1608Metric |  | CAP CER 22UF 6.3V X5R 0603 |  | GRM188R60J226MEA0D | 1 | 1 | 1 | 490-7611-1-ND | 0.19400
 |  | C705 | 2.2uF | servo:Capacitor | servo:C_0603_1608Metric |  | CAP CER 2.2UF 16V X6S 0603 |  | GRT188C81C225KE13D | 1 | 1 | 1 | 490-12287-1-ND | 0.35500
 |  | C708 | 22uF | servo:Capacitor | servo:C_0603_1608Metric |  | CAP CER 22UF 6.3V X5R 0603 |  | GRM188R60J226MEA0D | 1 | 1 | 1 | 490-7611-1-ND | 0.19400
 |  | C710 | 2.2uF | servo:Capacitor | servo:C_0603_1608Metric |  | CAP CER 2.2UF 16V X6S 0603 |  | GRT188C81C225KE13D | 1 | 1 | 1 | 490-12287-1-ND | 0.35500
 |  | C712 | 10uF | servo:Capacitor | servo:C_0603_1608Metric |  | 10µF ±20% 10V Ceramic Capacitor X5R 0603 (1608 Metric) |  | GRM188R61A106ME69D | 1 | 1 | 1 | 490-10475-1-ND | 0.15400
 |  | C714 | 0.1uF | servo:Capacitor | servo:C_0603_1608Metric |  | CAP CER 0.1UF 16V X7R 0603 |  | CC0603KPX7R7BB104 | 1 | 1 | 1 | 311-1335-1-ND | 0.05800
 |  | C801 | 100pF | servo:Capacitor | servo:C_0603_1608Metric |  | CAP CER 100PF 10V X7R 0603 |  | 885012206003 | 1 | 1 | 1 | 732-7922-1-ND | 0.02100
 |  | C802 | 100pF | servo:Capacitor | servo:C_0603_1608Metric |  | CAP CER 100PF 10V X7R 0603 |  | 885012206003 | 1 | 1 | 1 | 732-7922-1-ND | 0.02100
 |  | C803 | 100pF | servo:Capacitor | servo:C_0603_1608Metric |  | CAP CER 100PF 10V X7R 0603 |  | 885012206003 | 1 | 1 | 1 | 732-7922-1-ND | 0.02100
 |  | C804 | 100pF | servo:Capacitor | servo:C_0603_1608Metric |  | CAP CER 100PF 10V X7R 0603 |  | 885012206003 | 1 | 1 | 1 | 732-7922-1-ND | 0.02100
 |  | C805 | 100pF | servo:Capacitor | servo:C_0603_1608Metric |  | CAP CER 100PF 10V X7R 0603 |  | 885012206003 | 1 | 1 | 1 | 732-7922-1-ND | 0.02100
 |  | C806 | 100pF | servo:Capacitor | servo:C_0603_1608Metric |  | CAP CER 100PF 10V X7R 0603 |  | 885012206003 | 1 | 1 | 1 | 732-7922-1-ND | 0.02100
 |  | C807 | 100pF | servo:Capacitor | servo:C_0603_1608Metric |  | CAP CER 100PF 10V X7R 0603 |  | 885012206003 | 1 | 1 | 1 | 732-7922-1-ND | 0.02100
 |  | C808 | 100pF | servo:Capacitor | servo:C_0603_1608Metric |  | CAP CER 100PF 10V X7R 0603 |  | 885012206003 | 1 | 1 | 1 | 732-7922-1-ND | 0.02100
 |  | C809 | 100pF | servo:Capacitor | servo:C_0603_1608Metric |  | CAP CER 100PF 10V X7R 0603 |  | 885012206003 | 1 | 1 | 1 | 732-7922-1-ND | 0.02100
 |  | C810 | 100pF | servo:Capacitor | servo:C_0603_1608Metric |  | CAP CER 100PF 10V X7R 0603 |  | 885012206003 | 1 | 1 | 1 | 732-7922-1-ND | 0.02100
 |  | C811 | 100pF | servo:Capacitor | servo:C_0603_1608Metric |  | CAP CER 100PF 10V X7R 0603 |  | 885012206003 | 1 | 1 | 1 | 732-7922-1-ND | 0.02100
 |  | C812 | 100pF | servo:Capacitor | servo:C_0603_1608Metric |  | CAP CER 100PF 10V X7R 0603 |  | 885012206003 | 1 | 1 | 1 | 732-7922-1-ND | 0.02100
 |  | C813 | 100pF | servo:Capacitor | servo:C_0603_1608Metric |  | CAP CER 100PF 10V X7R 0603 |  | 885012206003 | 1 | 1 | 1 | 732-7922-1-ND | 0.02100
 |  | C814 | 100pF | servo:Capacitor | servo:C_0603_1608Metric |  | CAP CER 100PF 10V X7R 0603 |  | 885012206003 | 1 | 1 | 1 | 732-7922-1-ND | 0.02100
 |  | C815 | 100pF | servo:Capacitor | servo:C_0603_1608Metric |  | CAP CER 100PF 10V X7R 0603 |  | 885012206003 | 1 | 1 | 1 | 732-7922-1-ND | 0.02100
 |  | C816 | 100pF | servo:Capacitor | servo:C_0603_1608Metric |  | CAP CER 100PF 10V X7R 0603 |  | 885012206003 | 1 | 1 | 1 | 732-7922-1-ND | 0.02100
 |  | C817 | 100pF | servo:Capacitor | servo:C_0603_1608Metric |  | CAP CER 100PF 10V X7R 0603 |  | 885012206003 | 1 | 1 | 1 | 732-7922-1-ND | 0.02100
 |  | C818 | 100pF | servo:Capacitor | servo:C_0603_1608Metric |  | CAP CER 100PF 10V X7R 0603 |  | 885012206003 | 1 | 1 | 1 | 732-7922-1-ND | 0.02100
 |  | C819 | 100pF | servo:Capacitor | servo:C_0603_1608Metric |  | CAP CER 100PF 10V X7R 0603 |  | 885012206003 | 1 | 1 | 1 | 732-7922-1-ND | 0.02100
 |  | C820 | 100pF | servo:Capacitor | servo:C_0603_1608Metric |  | CAP CER 100PF 10V X7R 0603 |  | 885012206003 | 1 | 1 | 1 | 732-7922-1-ND | 0.02100
 |  | C821 | 100pF | servo:Capacitor | servo:C_0603_1608Metric |  | CAP CER 100PF 10V X7R 0603 |  | 885012206003 | 1 | 1 | 1 | 732-7922-1-ND | 0.02100
 |  | C822 | 100pF | servo:Capacitor | servo:C_0603_1608Metric |  | CAP CER 100PF 10V X7R 0603 |  | 885012206003 | 1 | 1 | 1 | 732-7922-1-ND | 0.02100
 |  | C823 | 100pF | servo:Capacitor | servo:C_0603_1608Metric |  | CAP CER 100PF 10V X7R 0603 |  | 885012206003 | 1 | 1 | 1 | 732-7922-1-ND | 0.02100
 |  | C824 | 100pF | servo:Capacitor | servo:C_0603_1608Metric |  | CAP CER 100PF 10V X7R 0603 |  | 885012206003 | 1 | 1 | 1 | 732-7922-1-ND | 0.02100
 |  | C825 | 0.1uF | servo:Capacitor | servo:C_0603_1608Metric |  | CAP CER 0.1UF 16V X7R 0603 |  | CC0603KPX7R7BB104 | 1 | 1 | 1 | 311-1335-1-ND | 0.05800
 |  | C826 | 0.1uF | servo:Capacitor | servo:C_0603_1608Metric |  | CAP CER 0.1UF 16V X7R 0603 |  | CC0603KPX7R7BB104 | 1 | 1 | 1 | 311-1335-1-ND | 0.05800
 |  | C828 | 0.1uF | servo:Capacitor | servo:C_0603_1608Metric |  | CAP CER 0.1UF 16V X7R 0603 |  | CC0603KPX7R7BB104 | 1 | 1 | 1 | 311-1335-1-ND | 0.05800
 |  | C829 | 0.1uF | servo:Capacitor | servo:C_0603_1608Metric |  | CAP CER 0.1UF 16V X7R 0603 |  | CC0603KPX7R7BB104 | 1 | 1 | 1 | 311-1335-1-ND | 0.05800
 |  | C830 | 0.1uF | servo:Capacitor | servo:C_0603_1608Metric |  | CAP CER 0.1UF 16V X7R 0603 |  | CC0603KPX7R7BB104 | 1 | 1 | 1 | 311-1335-1-ND | 0.05800
 |  | C831 | 0.1uF | servo:Capacitor | servo:C_0603_1608Metric |  | CAP CER 0.1UF 16V X7R 0603 |  | CC0603KPX7R7BB104 | 1 | 1 | 1 | 311-1335-1-ND | 0.05800
 |  | C832 | 0.1uF | servo:Capacitor | servo:C_0603_1608Metric |  | CAP CER 0.1UF 16V X7R 0603 |  | CC0603KPX7R7BB104 | 1 | 1 | 1 | 311-1335-1-ND | 0.05800
 |  | C833 | 0.1uF | servo:Capacitor | servo:C_0603_1608Metric |  | CAP CER 0.1UF 16V X7R 0603 |  | CC0603KPX7R7BB104 | 1 | 1 | 1 | 311-1335-1-ND | 0.05800
 |  | C834 | 0.1uF | servo:Capacitor | servo:C_0603_1608Metric |  | CAP CER 0.1UF 16V X7R 0603 |  | CC0603KPX7R7BB104 | 1 | 1 | 1 | 311-1335-1-ND | 0.05800
 |  | C835 | 0.1uF | servo:Capacitor | servo:C_0603_1608Metric |  | CAP CER 0.1UF 16V X7R 0603 |  | CC0603KPX7R7BB104 | 1 | 1 | 1 | 311-1335-1-ND | 0.05800
 |  | C836 | 0.1uF | servo:Capacitor | servo:C_0603_1608Metric |  | CAP CER 0.1UF 16V X7R 0603 |  | CC0603KPX7R7BB104 | 1 | 1 | 1 | 311-1335-1-ND | 0.05800
 |  | C837 | 0.1uF | servo:Capacitor | servo:C_0603_1608Metric |  | CAP CER 0.1UF 16V X7R 0603 |  | CC0603KPX7R7BB104 | 1 | 1 | 1 | 311-1335-1-ND | 0.05800
 |  | C838 | 0.1uF | servo:Capacitor | servo:C_0603_1608Metric |  | CAP CER 0.1UF 16V X7R 0603 |  | CC0603KPX7R7BB104 | 1 | 1 | 1 | 311-1335-1-ND | 0.05800
 |  | C839 | 0.1uF | servo:Capacitor | servo:C_0603_1608Metric |  | CAP CER 0.1UF 16V X7R 0603 |  | CC0603KPX7R7BB104 | 1 | 1 | 1 | 311-1335-1-ND | 0.05800
 |  | C840 | 0.1uF | servo:Capacitor | servo:C_0603_1608Metric |  | CAP CER 0.1UF 16V X7R 0603 |  | CC0603KPX7R7BB104 | 1 | 1 | 1 | 311-1335-1-ND | 0.05800
 |  | C841 | 0.1uF | servo:Capacitor | servo:C_0603_1608Metric |  | CAP CER 0.1UF 16V X7R 0603 |  | CC0603KPX7R7BB104 | 1 | 1 | 1 | 311-1335-1-ND | 0.05800
 |  | C842 | 0.1uF | servo:Capacitor | servo:C_0603_1608Metric |  | CAP CER 0.1UF 16V X7R 0603 |  | CC0603KPX7R7BB104 | 1 | 1 | 1 | 311-1335-1-ND | 0.05800
 |  | C901 | 0.1uF | servo:Capacitor | servo:C_0603_1608Metric |  | CAP CER 0.1UF 16V X7R 0603 |  | CC0603KPX7R7BB104 | 1 | 1 | 1 | 311-1335-1-ND | 0.05800
 |  | C902 | 0.1uF | servo:Capacitor | servo:C_0603_1608Metric |  | CAP CER 0.1UF 16V X7R 0603 |  | CC0603KPX7R7BB104 | 1 | 1 | 1 | 311-1335-1-ND | 0.05800
 |  | C903 | 0.1uF | servo:Capacitor | servo:C_0603_1608Metric |  | CAP CER 0.1UF 16V X7R 0603 |  | CC0603KPX7R7BB104 | 1 | 1 | 1 | 311-1335-1-ND | 0.05800
 |  | C904 | 0.1uF | servo:Capacitor | servo:C_0603_1608Metric |  | CAP CER 0.1UF 16V X7R 0603 |  | CC0603KPX7R7BB104 | 1 | 1 | 1 | 311-1335-1-ND | 0.05800
 |  | C905 | 0.1uF | servo:Capacitor | servo:C_0603_1608Metric |  | CAP CER 0.1UF 16V X7R 0603 |  | CC0603KPX7R7BB104 | 1 | 1 | 1 | 311-1335-1-ND | 0.05800
 |  | C906 | 0.1uF | servo:Capacitor | servo:C_0603_1608Metric |  | CAP CER 0.1UF 16V X7R 0603 |  | CC0603KPX7R7BB104 | 1 | 1 | 1 | 311-1335-1-ND | 0.05800
 |  | C907 | 0.1uF | servo:Capacitor | servo:C_0603_1608Metric |  | CAP CER 0.1UF 16V X7R 0603 |  | CC0603KPX7R7BB104 | 1 | 1 | 1 | 311-1335-1-ND | 0.05800
 |  | C908 | 0.1uF | servo:Capacitor | servo:C_0603_1608Metric |  | CAP CER 0.1UF 16V X7R 0603 |  | CC0603KPX7R7BB104 | 1 | 1 | 1 | 311-1335-1-ND | 0.05800
 |  | C909 | 0.1uF | servo:Capacitor | servo:C_0603_1608Metric |  | CAP CER 0.1UF 16V X7R 0603 |  | CC0603KPX7R7BB104 | 1 | 1 | 1 | 311-1335-1-ND | 0.05800
 |  | C910 | 0.1uF | servo:Capacitor | servo:C_0603_1608Metric |  | CAP CER 0.1UF 16V X7R 0603 |  | CC0603KPX7R7BB104 | 1 | 1 | 1 | 311-1335-1-ND | 0.05800
 |  | C911 | 0.1uF | servo:Capacitor | servo:C_0603_1608Metric |  | CAP CER 0.1UF 16V X7R 0603 |  | CC0603KPX7R7BB104 | 1 | 1 | 1 | 311-1335-1-ND | 0.05800
 |  | C912 | 0.1uF | servo:Capacitor | servo:C_0603_1608Metric |  | CAP CER 0.1UF 16V X7R 0603 |  | CC0603KPX7R7BB104 | 1 | 1 | 1 | 311-1335-1-ND | 0.05800
 |  | C913 | 0.1uF | servo:Capacitor | servo:C_0603_1608Metric |  | CAP CER 0.1UF 16V X7R 0603 |  | CC0603KPX7R7BB104 | 1 | 1 | 1 | 311-1335-1-ND | 0.05800
 |  | C914 | 0.1uF | servo:Capacitor | servo:C_0603_1608Metric |  | CAP CER 0.1UF 16V X7R 0603 |  | CC0603KPX7R7BB104 | 1 | 1 | 1 | 311-1335-1-ND | 0.05800
 |  | C915 | 0.1uF | servo:Capacitor | servo:C_0603_1608Metric |  | CAP CER 0.1UF 16V X7R 0603 |  | CC0603KPX7R7BB104 | 1 | 1 | 1 | 311-1335-1-ND | 0.05800
 |  | C916 | 0.1uF | servo:Capacitor | servo:C_0603_1608Metric |  | CAP CER 0.1UF 16V X7R 0603 |  | CC0603KPX7R7BB104 | 1 | 1 | 1 | 311-1335-1-ND | 0.05800
 |  | C917 | 0.1uF | servo:Capacitor | servo:C_0603_1608Metric |  | CAP CER 0.1UF 16V X7R 0603 |  | CC0603KPX7R7BB104 | 1 | 1 | 1 | 311-1335-1-ND | 0.05800
 |  | C918 | 0.1uF | servo:Capacitor | servo:C_0603_1608Metric |  | CAP CER 0.1UF 16V X7R 0603 |  | CC0603KPX7R7BB104 | 1 | 1 | 1 | 311-1335-1-ND | 0.05800
 |  | C1001 | 0.1uF | servo:Capacitor | servo:C_0603_1608Metric |  | CAP CER 0.1UF 16V X7R 0603 |  | CC0603KPX7R7BB104 | 1 | 1 | 1 | 311-1335-1-ND | 0.05800
 |  | C1101 | 0.1uF | servo:Capacitor | servo:C_0603_1608Metric |  | CAP CER 0.1UF 16V X7R 0603 |  | CC0603KPX7R7BB104 | 1 | 1 | 1 | 311-1335-1-ND | 0.05800
 |  | C1102 | 0.1uF | servo:Capacitor | servo:C_0603_1608Metric |  | CAP CER 0.1UF 16V X7R 0603 |  | CC0603KPX7R7BB104 | 1 | 1 | 1 | 311-1335-1-ND | 0.05800
 |  | C1103 | 0.1uF | servo:Capacitor | servo:C_0603_1608Metric |  | CAP CER 0.1UF 16V X7R 0603 |  | CC0603KPX7R7BB104 | 1 | 1 | 1 | 311-1335-1-ND | 0.05800
 |  | C1104 | 0.1uF | servo:Capacitor | servo:C_0603_1608Metric |  | CAP CER 0.1UF 16V X7R 0603 |  | CC0603KPX7R7BB104 | 1 | 1 | 1 | 311-1335-1-ND | 0.05800
 |  | C1105 | 0.1uF | servo:Capacitor | servo:C_0603_1608Metric |  | CAP CER 0.1UF 16V X7R 0603 |  | CC0603KPX7R7BB104 | 1 | 1 | 1 | 311-1335-1-ND | 0.05800
 |  | C1106 | 0.1uF | servo:Capacitor | servo:C_0603_1608Metric |  | CAP CER 0.1UF 16V X7R 0603 |  | CC0603KPX7R7BB104 | 1 | 1 | 1 | 311-1335-1-ND | 0.05800
 |  | C1201 | 0.1uF | servo:Capacitor | servo:C_0603_1608Metric |  | CAP CER 0.1UF 16V X7R 0603 |  | CC0603KPX7R7BB104 | 1 | 1 | 1 | 311-1335-1-ND | 0.05800
 |  | C1202 | 0.1uF | servo:Capacitor | servo:C_0603_1608Metric |  | CAP CER 0.1UF 16V X7R 0603 |  | CC0603KPX7R7BB104 | 1 | 1 | 1 | 311-1335-1-ND | 0.05800
 |  | C1203 | 0.1uF | servo:Capacitor | servo:C_0603_1608Metric |  | CAP CER 0.1UF 16V X7R 0603 |  | CC0603KPX7R7BB104 | 1 | 1 | 1 | 311-1335-1-ND | 0.05800
 |  | C1204 | 0.1uF | servo:Capacitor | servo:C_0603_1608Metric |  | CAP CER 0.1UF 16V X7R 0603 |  | CC0603KPX7R7BB104 | 1 | 1 | 1 | 311-1335-1-ND | 0.05800
 |  | C1401 | 10nF | servo:Capacitor | servo:C_0603_1608Metric |  | CAP CER 1000PF 16V X7R 0603 |  | 0603B102K160CT | 1 | 1 | 1 | 1292-1378-1-ND | 0.04100
 |  | C1403 | 47Uf | servo:Capacitor | servo:C_0603_1608Metric |  | 47µF ±20% 6.3V Ceramic Capacitor X5R 0603 (1608 Metric) |  | GRM188R60J476ME15D | 1 | 1 | 1 | 490-13247-6-ND | 0.46900
 |  | C1404 | 10uF | servo:Capacitor | servo:C_0603_1608Metric |  | 10µF ±20% 10V Ceramic Capacitor X5R 0603 (1608 Metric) |  | GRM188R61A106ME69D | 1 | 1 | 1 | 490-10475-1-ND | 0.15400
 |  | C1501 | 1nF | servo:Capacitor | servo:C_0603_1608Metric |  | CAP CER 1000PF 16V X7R 0603 |  | 0603B102K160CT | 1 | 1 | 1 | 1292-1378-1-ND | 0.04100
 |  | C1502 | 1nF | servo:Capacitor | servo:C_0603_1608Metric |  | CAP CER 1000PF 16V X7R 0603 |  | 0603B102K160CT | 1 | 1 | 1 | 1292-1378-1-ND | 0.04100
 |  | C1504 | 0.1uF | servo:Capacitor | servo:C_0603_1608Metric |  | CAP CER 0.1UF 16V X7R 0603 |  | CC0603KPX7R7BB104 | 1 | 1 | 1 | 311-1335-1-ND | 0.05800
 |  | C1505 | 0.1uF | servo:Capacitor | servo:C_0603_1608Metric |  | CAP CER 0.1UF 16V X7R 0603 |  | CC0603KPX7R7BB104 | 1 | 1 | 1 | 311-1335-1-ND | 0.05800
 |  | C1508 | 0.1uF | servo:Capacitor | servo:C_0603_1608Metric |  | CAP CER 0.1UF 16V X7R 0603 |  | CC0603KPX7R7BB104 | 1 | 1 | 1 | 311-1335-1-ND | 0.05800
 |  | C1509 | 1nF | servo:Capacitor | servo:C_0603_1608Metric |  | CAP CER 1000PF 16V X7R 0603 |  | 0603B102K160CT | 1 | 1 | 1 | 1292-1378-1-ND | 0.04100
 |  | C1510 | 0.1uF | servo:Capacitor | servo:C_0603_1608Metric |  | CAP CER 0.1UF 16V X7R 0603 |  | CC0603KPX7R7BB104 | 1 | 1 | 1 | 311-1335-1-ND | 0.05800
 |  | C1511 | 0.1uF | servo:Capacitor | servo:C_0603_1608Metric |  | CAP CER 0.1UF 16V X7R 0603 |  | CC0603KPX7R7BB104 | 1 | 1 | 1 | 311-1335-1-ND | 0.05800
 |  | C1512 | 0.1uF | servo:Capacitor | servo:C_0603_1608Metric |  | CAP CER 0.1UF 16V X7R 0603 |  | CC0603KPX7R7BB104 | 1 | 1 | 1 | 311-1335-1-ND | 0.05800
 |  | C1513 | 1nF | servo:Capacitor | servo:C_0603_1608Metric |  | CAP CER 1000PF 16V X7R 0603 |  | 0603B102K160CT | 1 | 1 | 1 | 1292-1378-1-ND | 0.04100
 |  | C1514 | 1nF | servo:Capacitor | servo:C_0603_1608Metric |  | CAP CER 1000PF 16V X7R 0603 |  | 0603B102K160CT | 1 | 1 | 1 | 1292-1378-1-ND | 0.04100
 |  | C1515 | 1nF | servo:Capacitor | servo:C_0603_1608Metric |  | CAP CER 1000PF 16V X7R 0603 |  | 0603B102K160CT | 1 | 1 | 1 | 1292-1378-1-ND | 0.04100
 |  | C1601 | 0.1uF | servo:Capacitor | servo:C_0603_1608Metric |  | CAP CER 0.1UF 16V X7R 0603 |  | CC0603KPX7R7BB104 | 1 | 1 | 1 | 311-1335-1-ND | 0.05800
 |  | C1602 | 0.1uF | servo:Capacitor | servo:C_0603_1608Metric |  | CAP CER 0.1UF 16V X7R 0603 |  | CC0603KPX7R7BB104 | 1 | 1 | 1 | 311-1335-1-ND | 0.05800
 |  | C1603 | 0.1uF | servo:Capacitor | servo:C_0603_1608Metric |  | CAP CER 0.1UF 16V X7R 0603 |  | CC0603KPX7R7BB104 | 1 | 1 | 1 | 311-1335-1-ND | 0.05800
 |  | C1604 | 0.1uF | servo:Capacitor | servo:C_0603_1608Metric |  | CAP CER 0.1UF 16V X7R 0603 |  | CC0603KPX7R7BB104 | 1 | 1 | 1 | 311-1335-1-ND | 0.05800
 |  | C1605 | 1nF | servo:Capacitor | servo:C_0603_1608Metric |  | CAP CER 1000PF 16V X7R 0603 |  | 0603B102K160CT | 1 | 1 | 1 | 1292-1378-1-ND | 0.04100
 |  | C1606 | 1nF | servo:Capacitor | servo:C_0603_1608Metric |  | CAP CER 1000PF 16V X7R 0603 |  | 0603B102K160CT | 1 | 1 | 1 | 1292-1378-1-ND | 0.04100
 |  | C1607 | 0.1uF | servo:Capacitor | servo:C_0603_1608Metric |  | CAP CER 0.1UF 16V X7R 0603 |  | CC0603KPX7R7BB104 | 1 | 1 | 1 | 311-1335-1-ND | 0.05800
 |  | C1608 | 0.1uF | servo:Capacitor | servo:C_0603_1608Metric |  | CAP CER 0.1UF 16V X7R 0603 |  | CC0603KPX7R7BB104 | 1 | 1 | 1 | 311-1335-1-ND | 0.05800
 |  | C1609 | 0.1uF | servo:Capacitor | servo:C_0603_1608Metric |  | CAP CER 0.1UF 16V X7R 0603 |  | CC0603KPX7R7BB104 | 1 | 1 | 1 | 311-1335-1-ND | 0.05800
 |  | C1610 | 0.1uF | servo:Capacitor | servo:C_0603_1608Metric |  | CAP CER 0.1UF 16V X7R 0603 |  | CC0603KPX7R7BB104 | 1 | 1 | 1 | 311-1335-1-ND | 0.05800
 |  | C1801 | 10pF | servo:Capacitor | servo:C_0603_1608Metric |  | CAP CER 10PF 16V C0G/NP0 0603 |  | 885012006017 | 1 | 1 | 1 | 732-7760-1-ND | 0.02500
 |  | C1802 | 10pF | servo:Capacitor | servo:C_0603_1608Metric |  | CAP CER 10PF 16V C0G/NP0 0603 |  | 885012006017 | 1 | 1 | 1 | 732-7760-1-ND | 0.02500
 |  | C1803 | 10pF | servo:Capacitor | servo:C_0603_1608Metric |  | CAP CER 10PF 16V C0G/NP0 0603 |  | 885012006017 | 1 | 1 | 1 | 732-7760-1-ND | 0.02500
 |  | C1804 | 10pF | servo:Capacitor | servo:C_0603_1608Metric |  | CAP CER 10PF 16V C0G/NP0 0603 |  | 885012006017 | 1 | 1 | 1 | 732-7760-1-ND | 0.02500
 |  | C1805 | 10pF | servo:Capacitor | servo:C_0603_1608Metric |  | CAP CER 10PF 16V C0G/NP0 0603 |  | 885012006017 | 1 | 1 | 1 | 732-7760-1-ND | 0.02500
 |  | C1806 | 10pF | servo:Capacitor | servo:C_0603_1608Metric |  | CAP CER 10PF 16V C0G/NP0 0603 |  | 885012006017 | 1 | 1 | 1 | 732-7760-1-ND | 0.02500
 |  | C1807 | 10pF | servo:Capacitor | servo:C_0603_1608Metric |  | CAP CER 10PF 16V C0G/NP0 0603 |  | 885012006017 | 1 | 1 | 1 | 732-7760-1-ND | 0.02500
 |  | C1808 | 10pF | servo:Capacitor | servo:C_0603_1608Metric |  | CAP CER 10PF 16V C0G/NP0 0603 |  | 885012006017 | 1 | 1 | 1 | 732-7760-1-ND | 0.02500
 |  | C1809 | 10pF | servo:Capacitor | servo:C_0603_1608Metric |  | CAP CER 10PF 16V C0G/NP0 0603 |  | 885012006017 | 1 | 1 | 1 | 732-7760-1-ND | 0.02500
 |  | C1810 | 10pF | servo:Capacitor | servo:C_0603_1608Metric |  | CAP CER 10PF 16V C0G/NP0 0603 |  | 885012006017 | 1 | 1 | 1 | 732-7760-1-ND | 0.02500
 |  | C1811 | 10pF | servo:Capacitor | servo:C_0603_1608Metric |  | CAP CER 10PF 16V C0G/NP0 0603 |  | 885012006017 | 1 | 1 | 1 | 732-7760-1-ND | 0.02500
 |  | C1812 | 10pF | servo:Capacitor | servo:C_0603_1608Metric |  | CAP CER 10PF 16V C0G/NP0 0603 |  | 885012006017 | 1 | 1 | 1 | 732-7760-1-ND | 0.02500
 |  | C1813 | 0.1uF | servo:Capacitor | servo:C_0603_1608Metric |  | CAP CER 0.1UF 16V X7R 0603 |  | CC0603KPX7R7BB104 | 1 | 1 | 1 | 311-1335-1-ND | 0.05800
 |  | C1814 | 0.1uF | servo:Capacitor | servo:C_0603_1608Metric |  | CAP CER 0.1UF 16V X7R 0603 |  | CC0603KPX7R7BB104 | 1 | 1 | 1 | 311-1335-1-ND | 0.05800
 |  | C1815 | 0.1uF | servo:Capacitor | servo:C_0603_1608Metric |  | CAP CER 0.1UF 16V X7R 0603 |  | CC0603KPX7R7BB104 | 1 | 1 | 1 | 311-1335-1-ND | 0.05800
 |  | C1816 | 0.1uF | servo:Capacitor | servo:C_0603_1608Metric |  | CAP CER 0.1UF 16V X7R 0603 |  | CC0603KPX7R7BB104 | 1 | 1 | 1 | 311-1335-1-ND | 0.05800
 |  | C1817 | 0.1uF | servo:Capacitor | servo:C_0603_1608Metric |  | CAP CER 0.1UF 16V X7R 0603 |  | CC0603KPX7R7BB104 | 1 | 1 | 1 | 311-1335-1-ND | 0.05800
 |  | C1818 | 0.1uF | servo:Capacitor | servo:C_0603_1608Metric |  | CAP CER 0.1UF 16V X7R 0603 |  | CC0603KPX7R7BB104 | 1 | 1 | 1 | 311-1335-1-ND | 0.05800
 |  | C1901 | 0.1uF | servo:Capacitor | servo:C_0603_1608Metric |  | CAP CER 0.1UF 16V X7R 0603 |  | CC0603KPX7R7BB104 | 1 | 1 | 1 | 311-1335-1-ND | 0.05800
 |  | C1904 | 0.1uF | servo:Capacitor | servo:C_0603_1608Metric |  | CAP CER 0.1UF 16V X7R 0603 |  | CC0603KPX7R7BB104 | 1 | 1 | 1 | 311-1335-1-ND | 0.05800
 |  | C1905 | 0.1uF | servo:Capacitor | servo:C_0603_1608Metric |  | CAP CER 0.1UF 16V X7R 0603 |  | CC0603KPX7R7BB104 | 1 | 1 | 1 | 311-1335-1-ND | 0.05800
 |  | C1910 | 0.1uF | servo:Capacitor | servo:C_0603_1608Metric |  | CAP CER 0.1UF 16V X7R 0603 |  | CC0603KPX7R7BB104 | 1 | 1 | 1 | 311-1335-1-ND | 0.05800
 |  | C1913 | 0.1uF | servo:Capacitor | servo:C_0603_1608Metric |  | CAP CER 0.1UF 16V X7R 0603 |  | CC0603KPX7R7BB104 | 1 | 1 | 1 | 311-1335-1-ND | 0.05800
 |  | C1914 | 0.1uF | servo:Capacitor | servo:C_0603_1608Metric |  | CAP CER 0.1UF 16V X7R 0603 |  | CC0603KPX7R7BB104 | 1 | 1 | 1 | 311-1335-1-ND | 0.05800
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

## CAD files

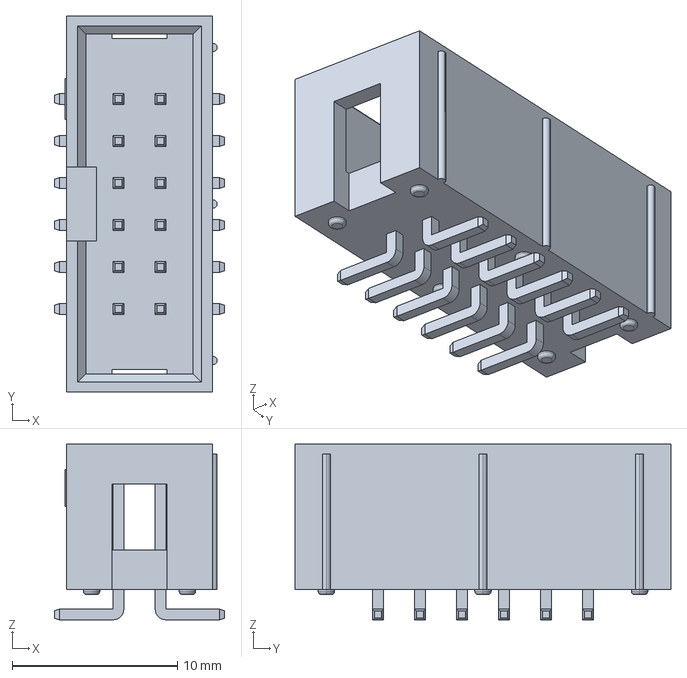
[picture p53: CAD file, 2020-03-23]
kicad/shapes3D/idc2x06_sm.stp
10.3 x 22.7 x 10.6 mm

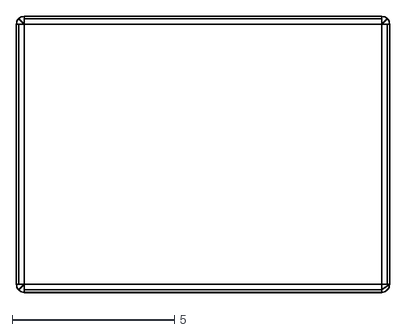
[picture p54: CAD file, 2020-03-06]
kicad/shapes3D/Converter_DCDC_RECOM_R-78B3.3-2.0_THT.dxf
11.5 x 8.51

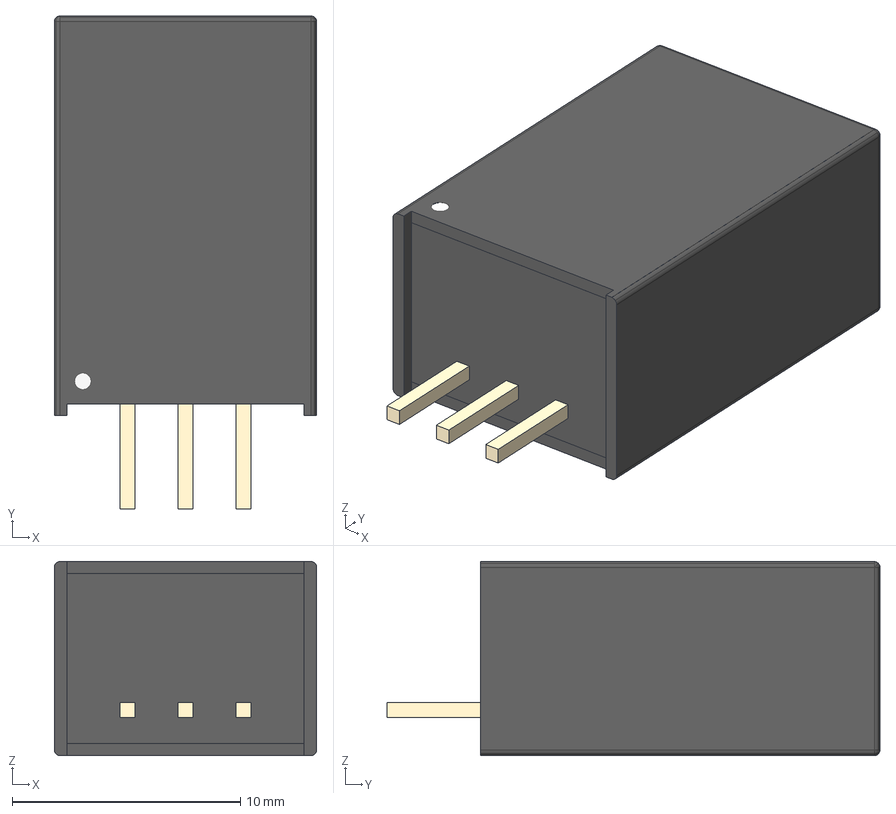
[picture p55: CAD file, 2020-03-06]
kicad/shapes3D/R-78B15-2.0--3DModel-STEP-1.STEP
11.5 x 21.6 x 8.51 mm

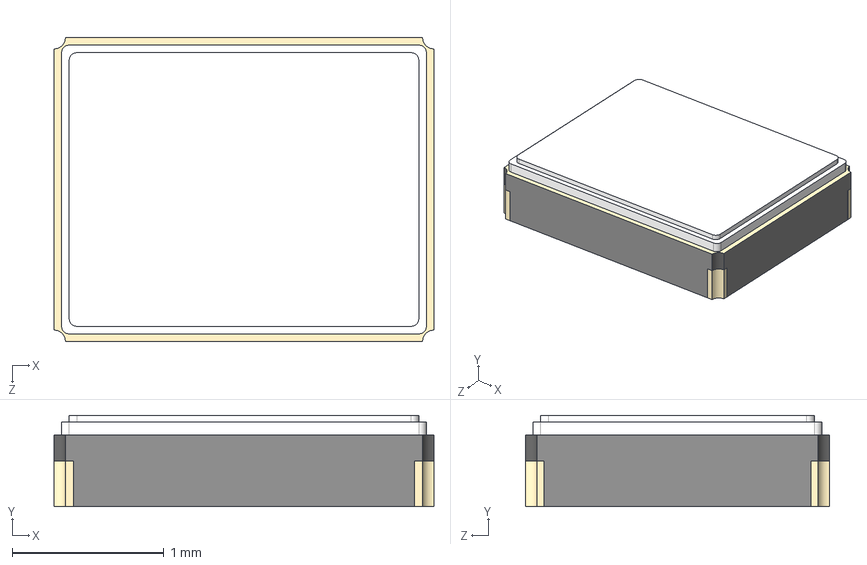
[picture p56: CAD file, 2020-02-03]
kicad/shapes3D/ECS-120-8-36-CKM-TR--3DModel-STEP-15126.STEP
2.50 x 0.6 x 2.00 mm

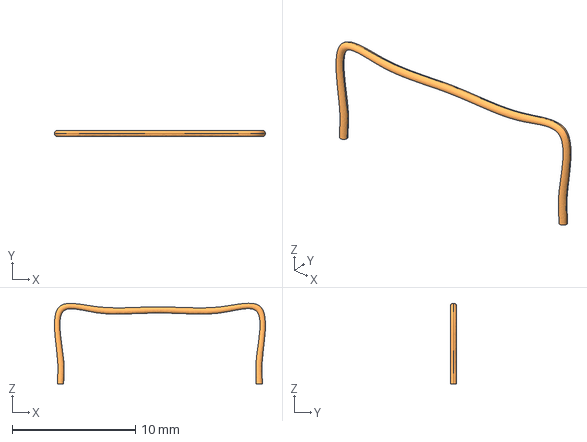
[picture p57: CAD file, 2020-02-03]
kicad/shapes3D/wire_bridge_16mm.stp
17.1 x 0.5 x 6.54 mm

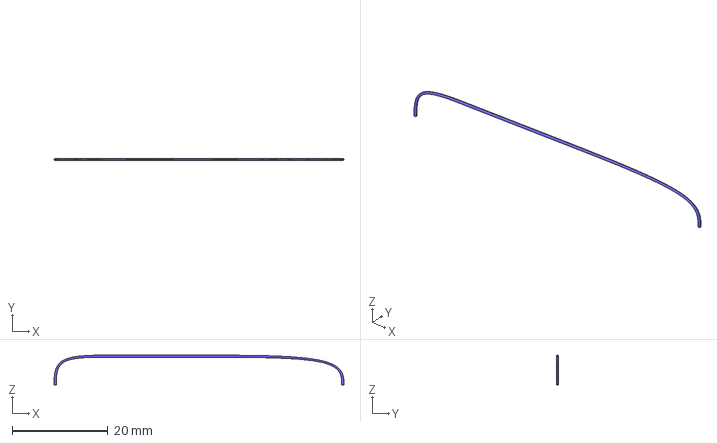
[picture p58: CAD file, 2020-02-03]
kicad/shapes3D/wire_bridge_60mm.stp
60.5 x 0.5 x 6.25 mm

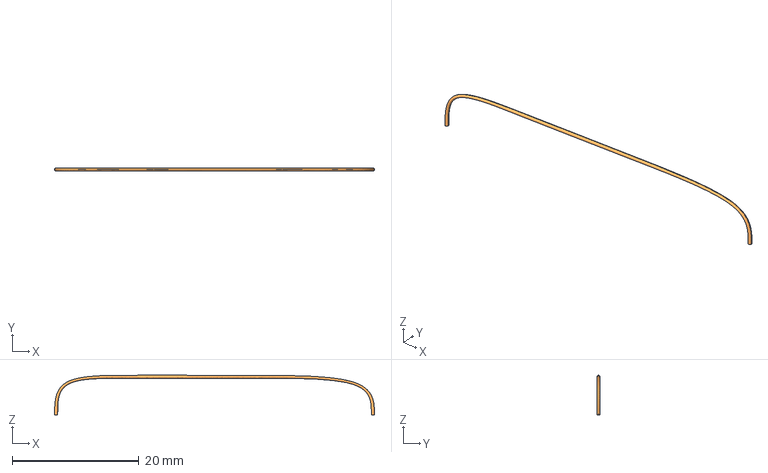
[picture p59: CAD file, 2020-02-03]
kicad/shapes3D/wire_bridge_50mm.stp
50.5 x 0.5 x 6.25 mm

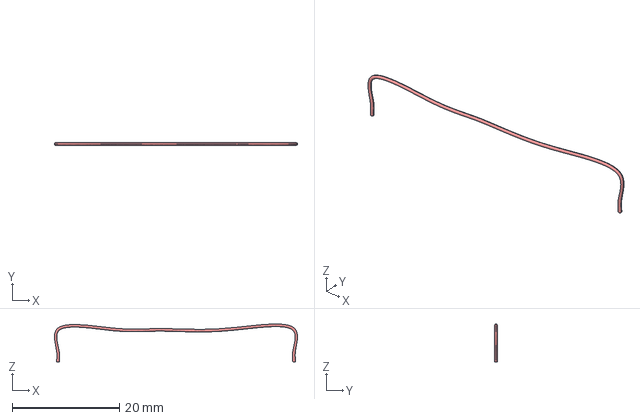
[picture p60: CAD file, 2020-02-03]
kicad/shapes3D/wire_bridge_44mm.stp
45.3 x 0.5 x 7.08 mm

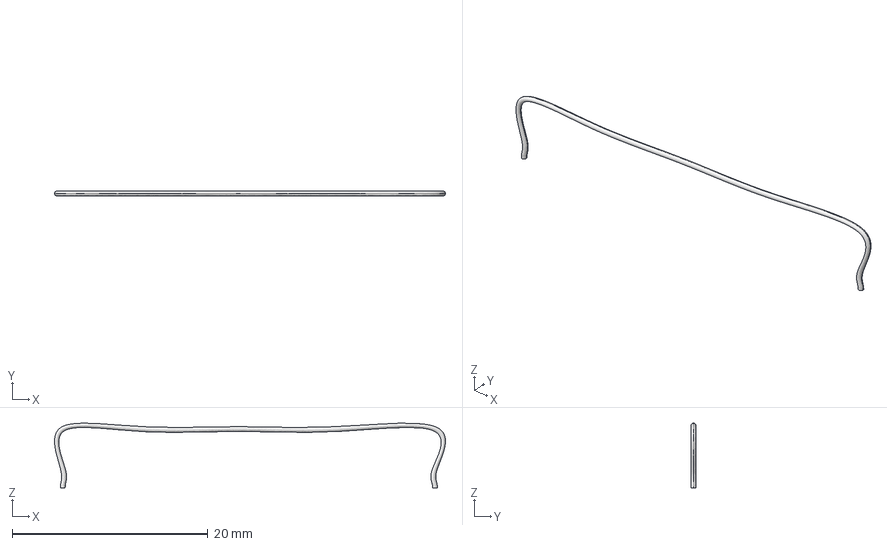
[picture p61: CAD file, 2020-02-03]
kicad/shapes3D/wire_bridge_38mm.stp
39.9 x 0.5 x 6.61 mm

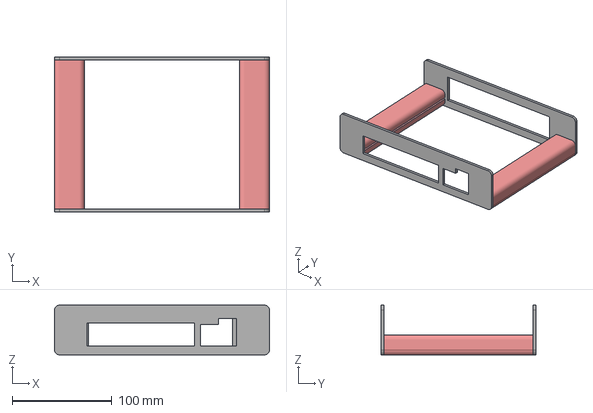
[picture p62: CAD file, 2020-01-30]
kicad/shapes3D/case.stp
216.0 x 156.0 x 50.0 mm

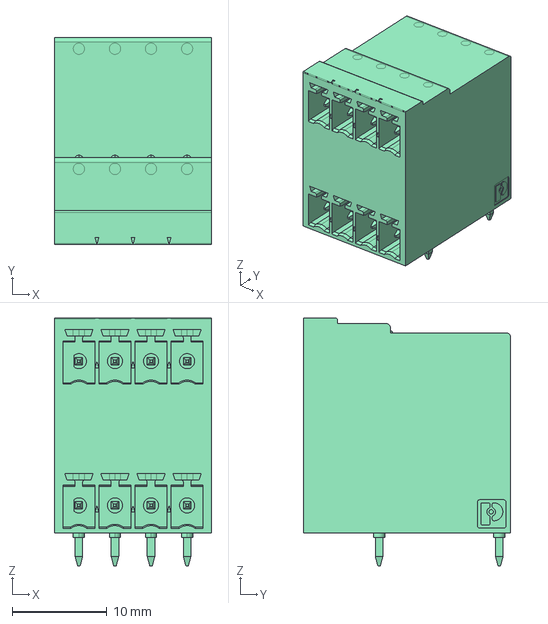
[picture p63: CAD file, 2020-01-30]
kicad/shapes3D/tblock2x4_3_81.stp
16.6 x 21.9 x 26.2 mm

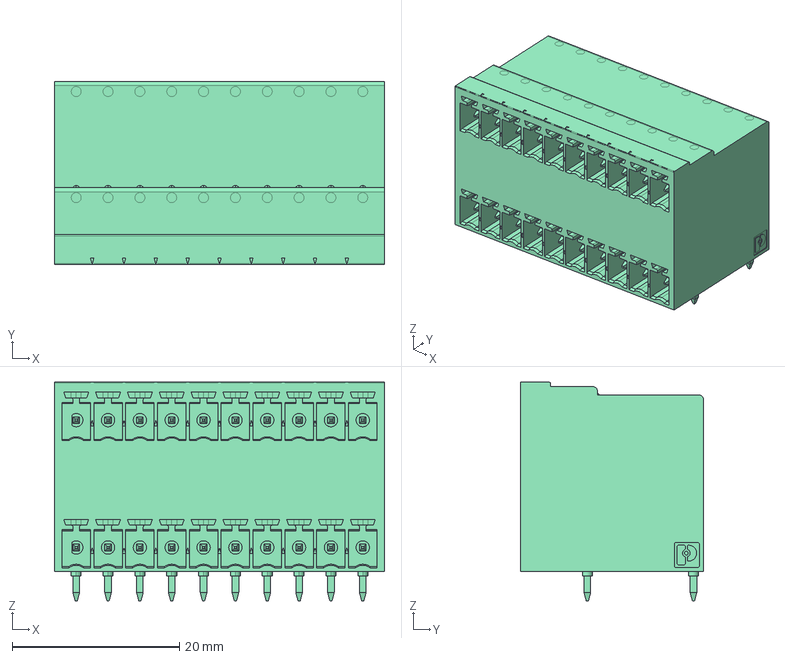
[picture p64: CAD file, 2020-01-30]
kicad/shapes3D/tblock2x10_3_81.stp
39.5 x 21.9 x 26.2 mm

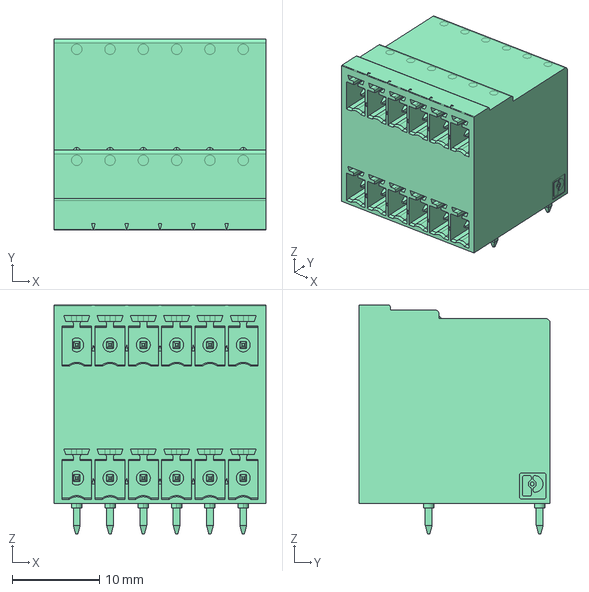
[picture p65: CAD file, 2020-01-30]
kicad/shapes3D/tblock2x6_3_81.stp
24.3 x 21.9 x 26.2 mm

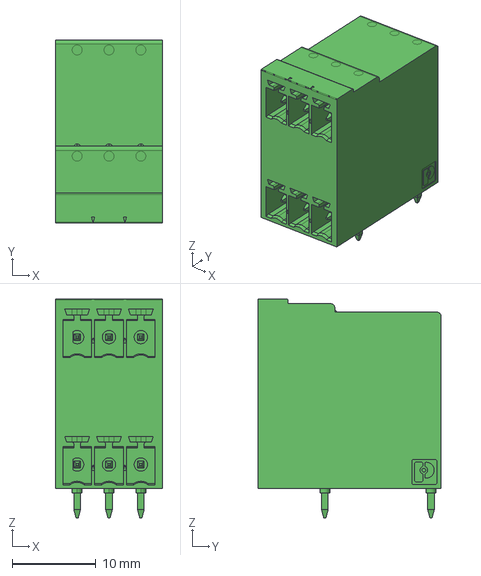
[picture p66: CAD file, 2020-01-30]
kicad/shapes3D/tblock2x3_3_81.stp
12.8 x 21.9 x 26.2 mm

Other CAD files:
kicad/shapes3D/SBH11-_ _ _C-D06-SM-_ _.STEP
kicad/shapes3D/lem_lxs.stp
kicad/shapes3D/idc2x17_sm.stp
kicad/shapes3D/idc2x10_sm.stp
kicad/shapes3D/0821-1X1T-36-F--3DModel-STEP-56544.STEP
kicad/shapes3D/ARJ11D.STEP
kicad/shapes3D/ARJ11D.dxf
kicad/shapes3D/ARJM11D7-009-AB.dxf
kicad/shapes3D/IDC-Header_2x10_P2.54mm_Vertical.step
kicad/shapes3D/bga337.stp
kicad/shapes3D/case.3dm
kicad/shapes3D/fuse_3912.dxf
kicad/shapes3D/fuse_3912.stp
kicad/shapes3D/idc2x06_smd.3dm
kicad/shapes3D/idc2x10_sm.dxf
kicad/shapes3D/idc2x10_smd.3dm
kicad/shapes3D/idc2x17_sm.dxf
kicad/shapes3D/idc2x17_smd.3dm
kicad/shapes3D/irm-10.stp
kicad/shapes3D/j45x2_dr-MAG-0845-2G1T-H5-1309698.3dm
kicad/shapes3D/j45x2_dr-MAG-0845-2G1T-H5-1309698.stp
kicad/shapes3D/lem_lxs.3dm
kicad/shapes3D/lem_lxs.dxf
kicad/shapes3D/puente_alambre.3dm
kicad/shapes3D/pxc_1736713_01_MDSTB-2-5-4-G1-5-08_3D.stp
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

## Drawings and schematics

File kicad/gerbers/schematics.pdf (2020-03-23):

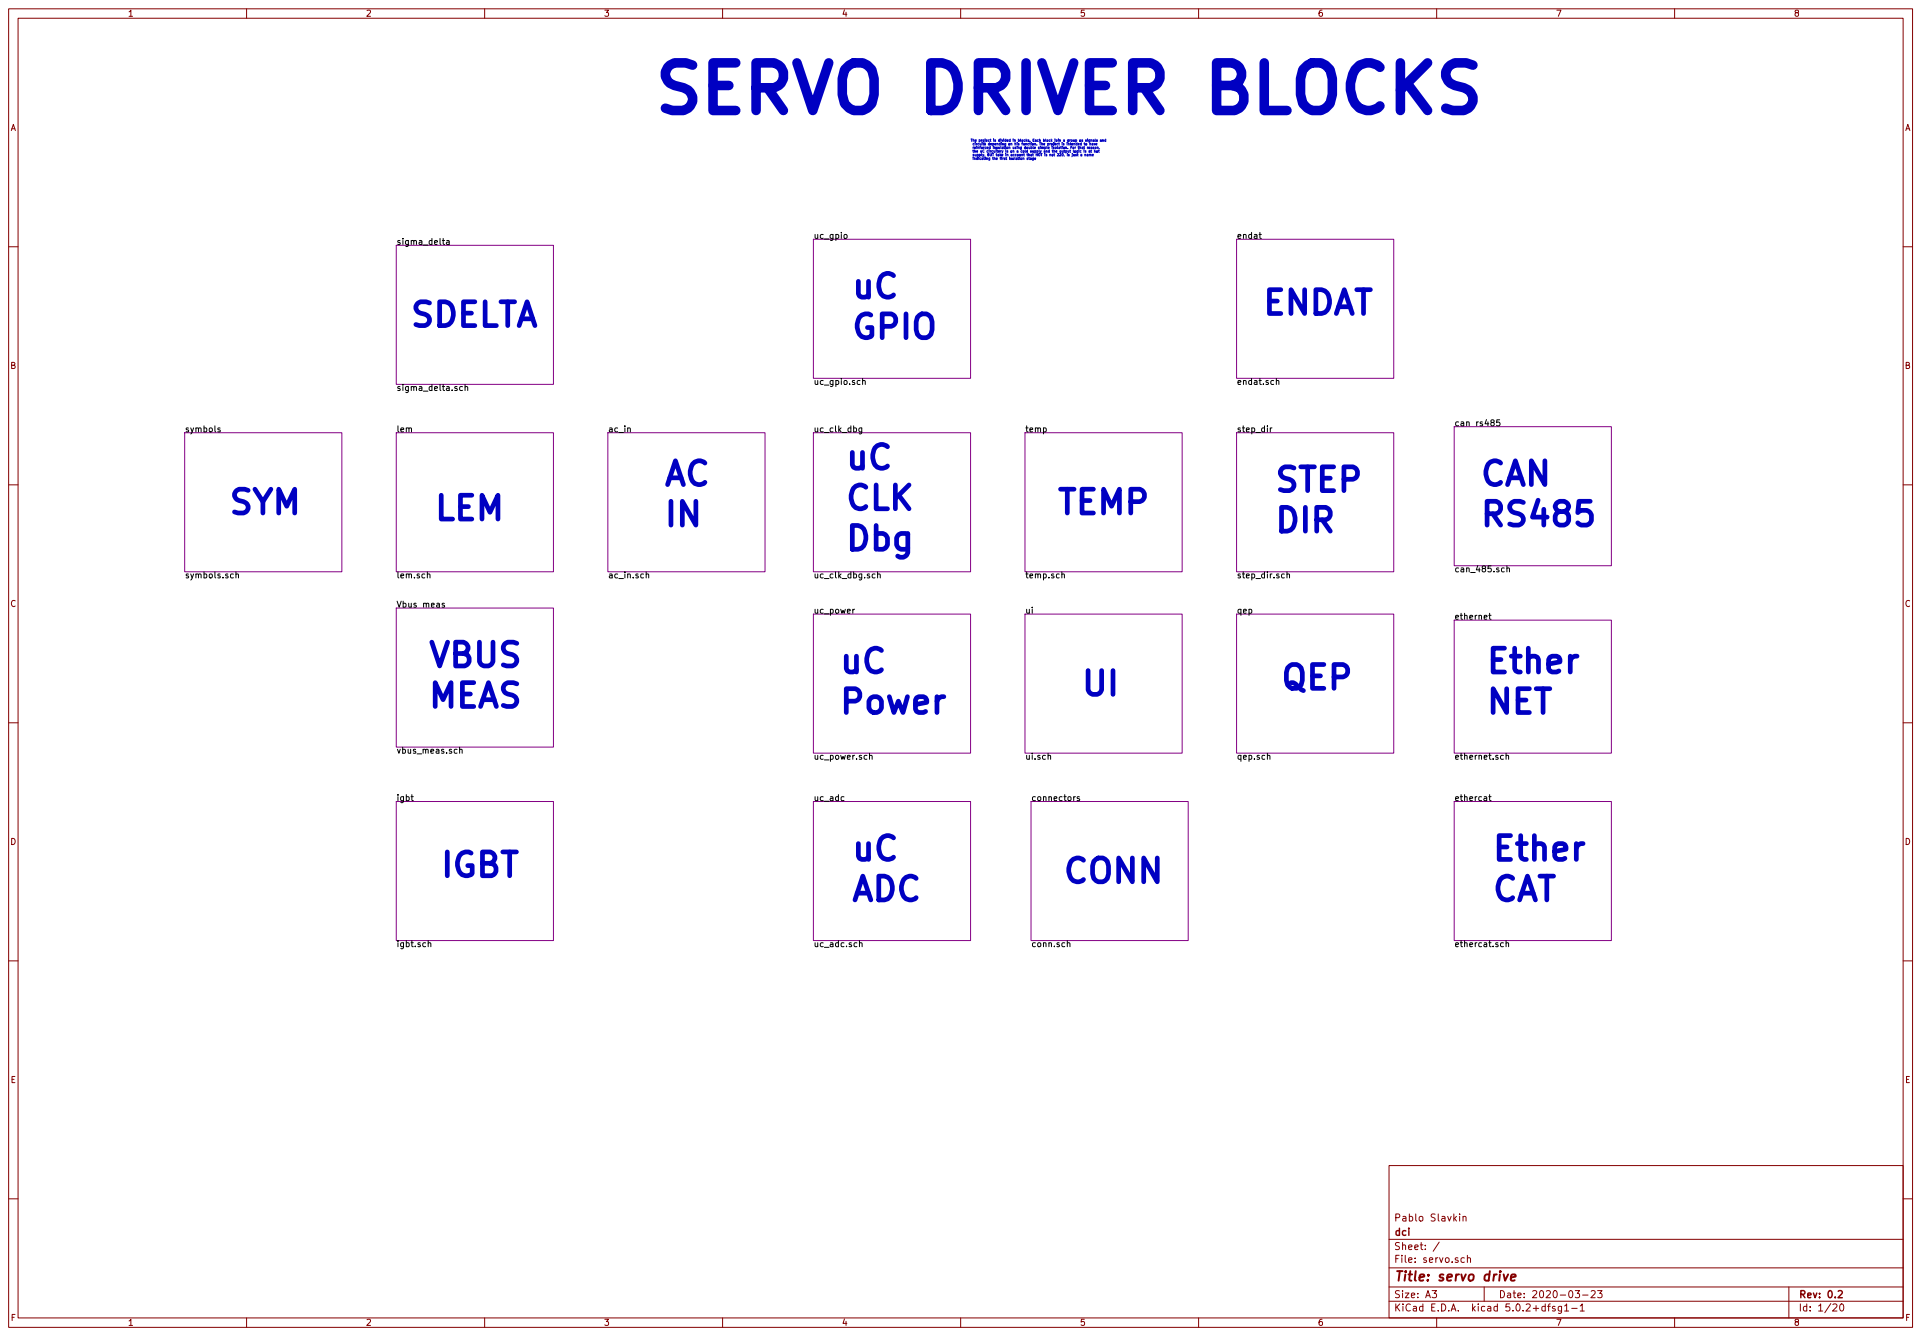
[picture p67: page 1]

SERVO DRIVER BLOCKS The project is divided in blocks. Each block join a group os signals and

circuits depending on his function. The project is intended to have
reinforced insulation using double simple isolation. For that reason,
the uC circuitery is on a cold supply and the output logic is at hot
supply, BUT take in account that HOT is not 220, is just a name

indicating the first isolation stage sigma_delta

File: servo.sch Sheet: / dci Pablo Slavkin

Id: 1/20 Title: servo drive

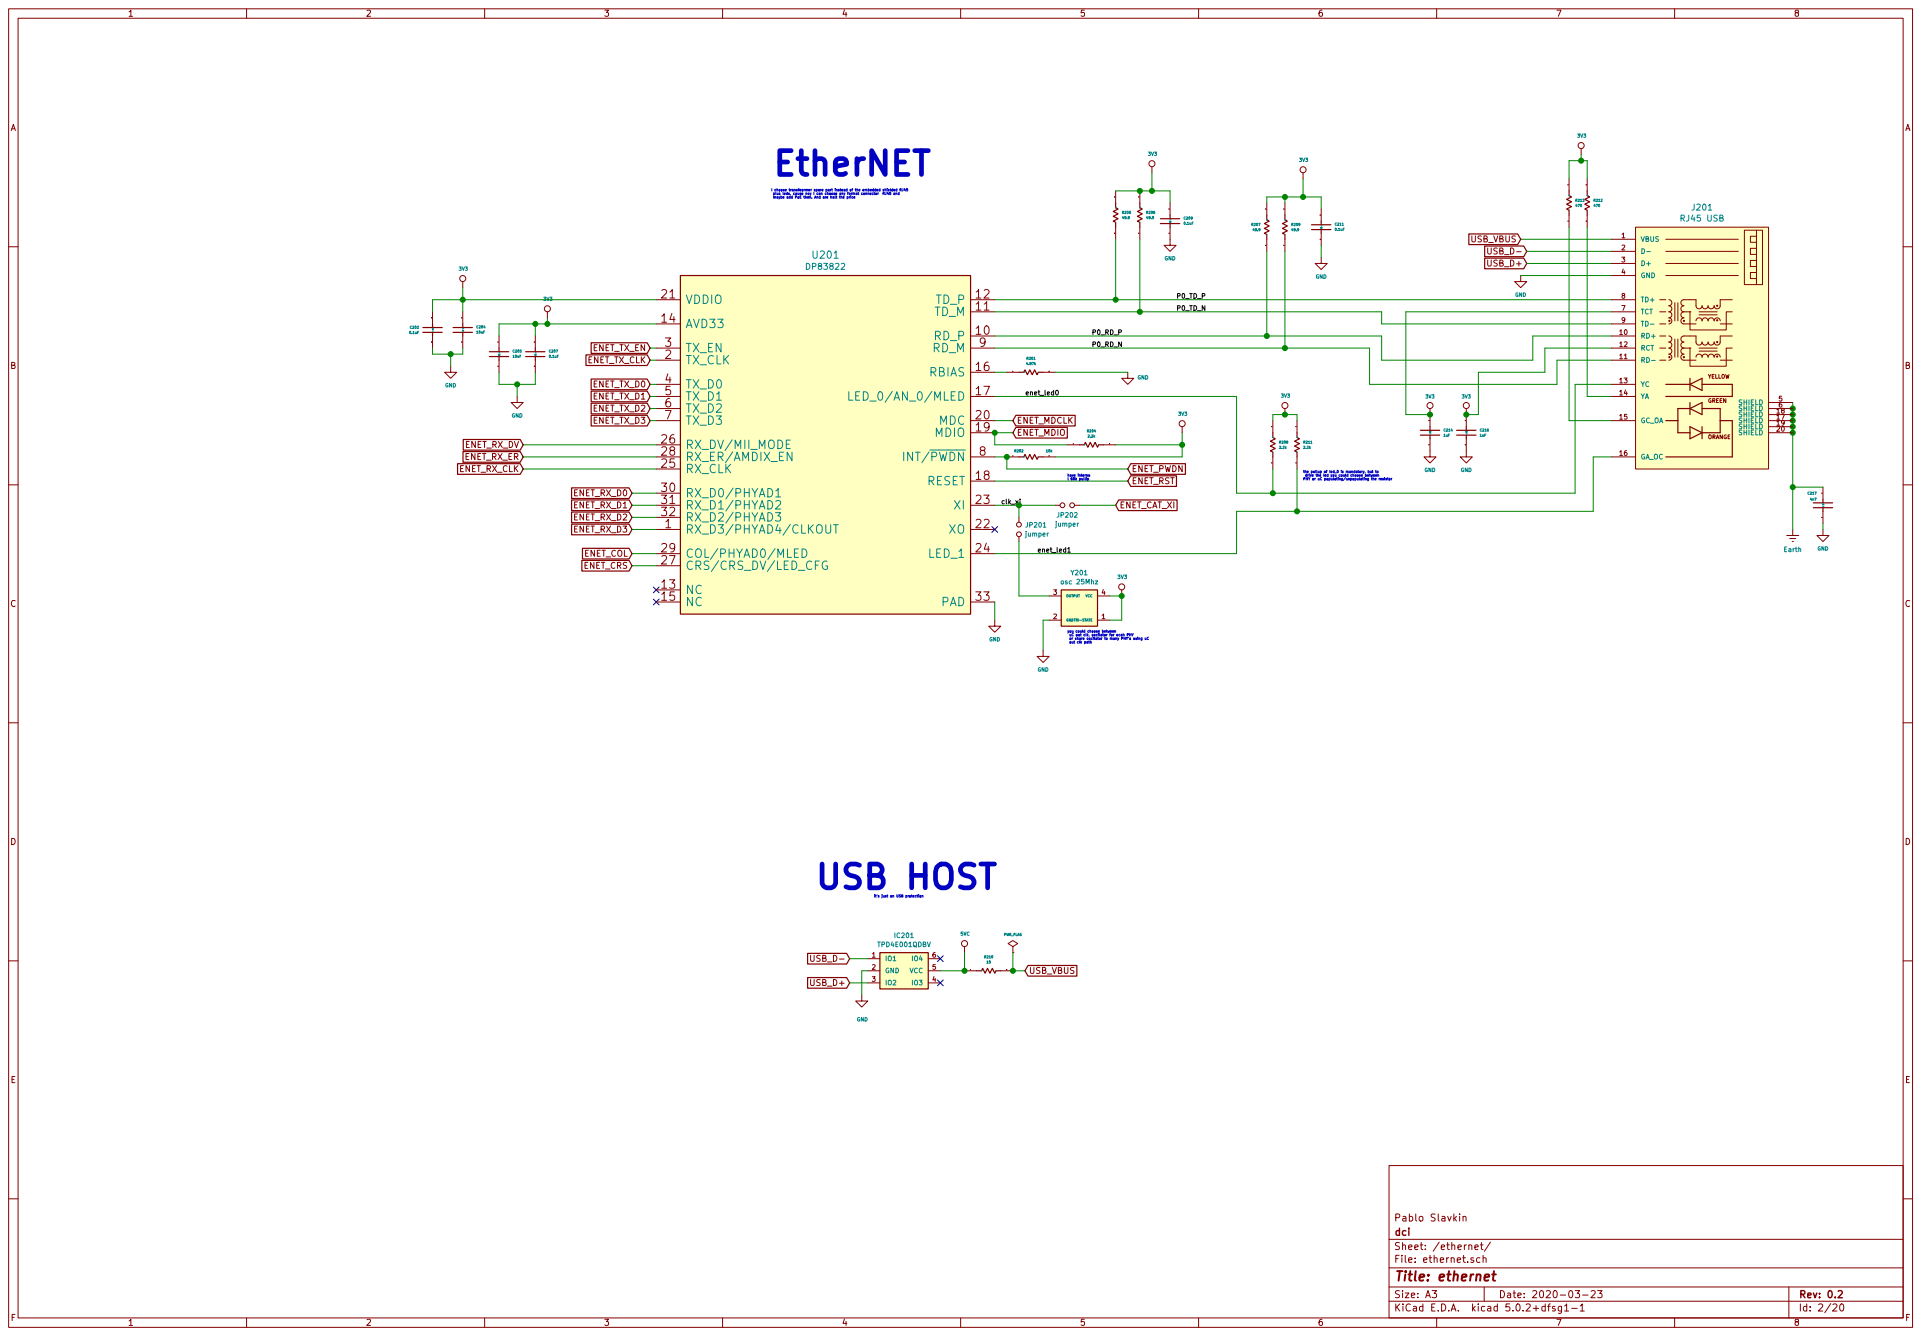
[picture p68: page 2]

I choose transfeormer spare part instead of the embedded shielded RJ45
plus leds, cause noy I can choose any format connector RJ45 and

AVD33 14 | P0_TD_N

P0_RD_P
P0_RD_N

the pullup of led_0 is mandatory, but to
drive the led you could choose between PHY or uC populating/unpopulating the resistor

you could choose between
uC out clk, oscilator for ecah PHY
or share oscilator to many PHY's using uC
out clk path

USB_D+ USB_D- USB HOST it's just an USB protection

Id: 2/20 Title: ethernet File: ethernet.sch Sheet: /ethernet/ dci Pablo Slavkin

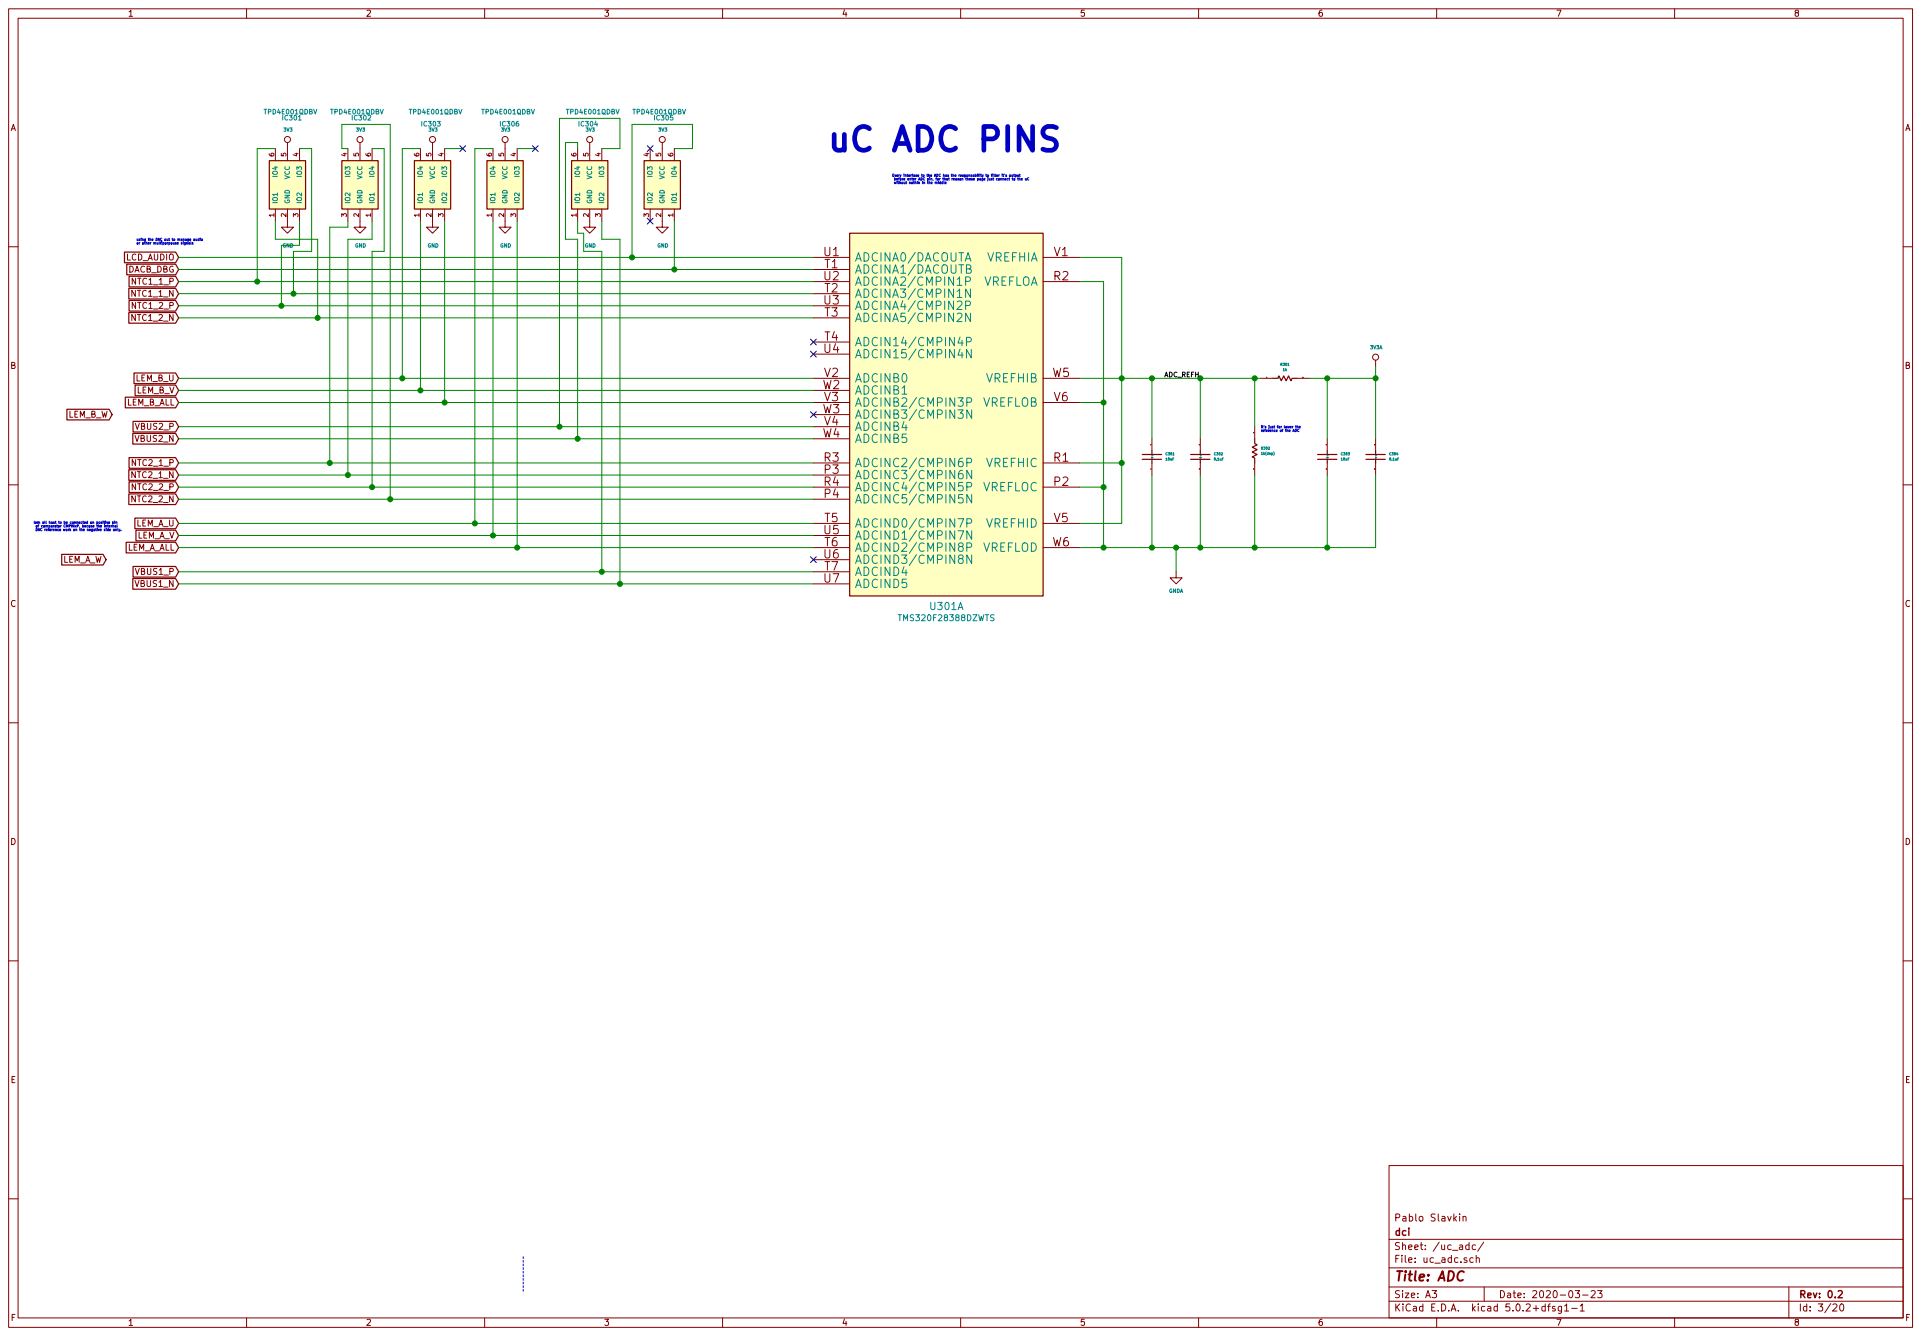
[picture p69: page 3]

without nothin in the middle LCD_AUDIO

Every interfase to the ADC has the responsability to filter it's output
before enter ADC pin, for that reason these page just connect to the uC

using the DAC out to manage audio or other multiporpouse signals DACB_DBG

1k LEM_A_U
it's just for lower the reference of the ADC ADC_REFH VBUS1_P
LEM_B_U
LEM_B_V

lem all hast to be connected on positive pin

Sheet: /uc_adc/ dci Pablo Slavkin

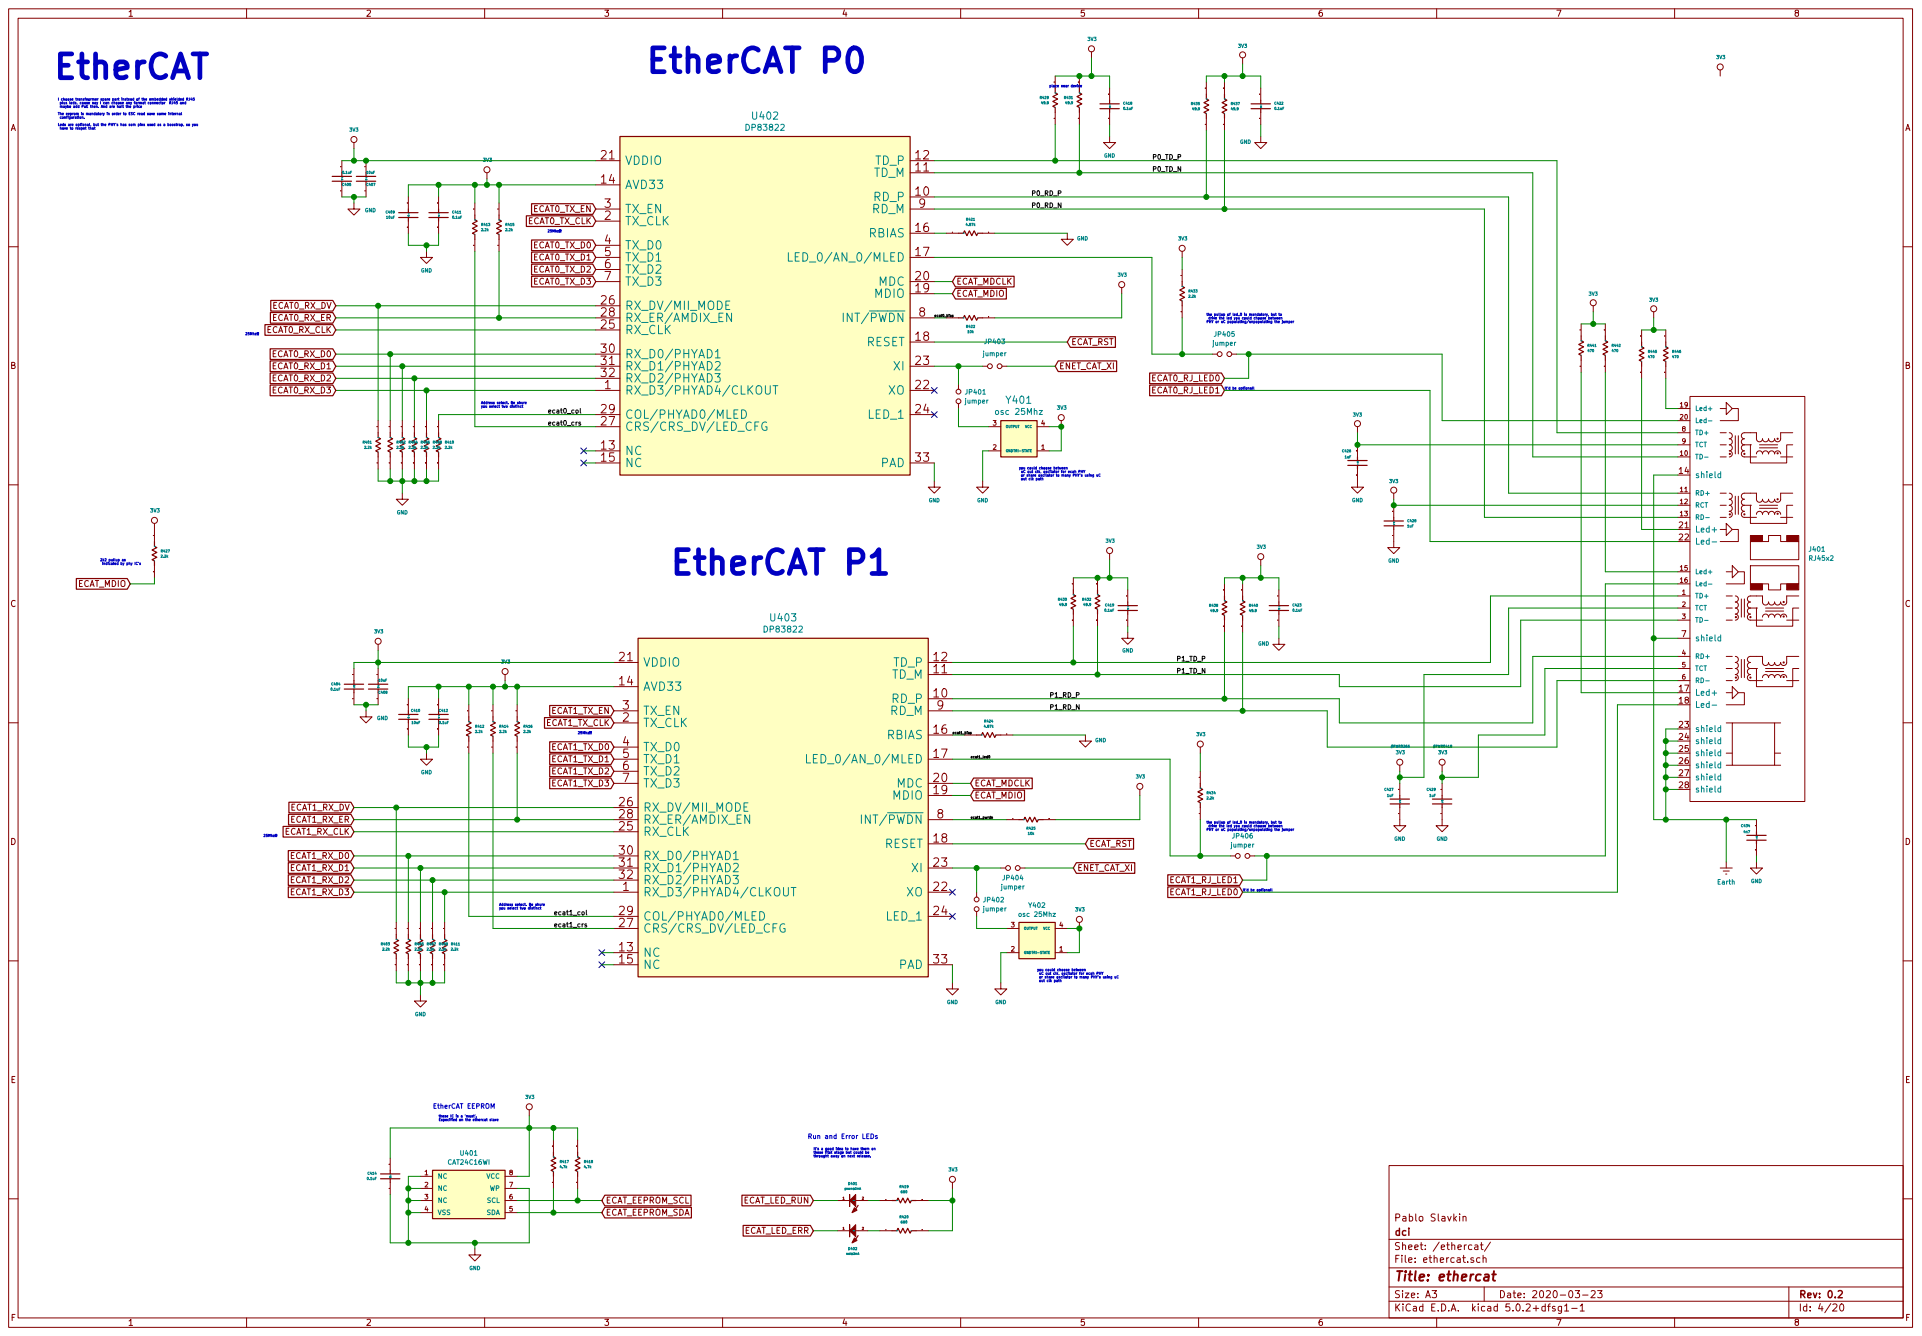
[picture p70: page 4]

these IC is a 'must'. Especified on the ethercat slave EtherCAT

I choose transfeormer spare part instead of the embedded shielded RJ45
plus leds, cause noy I can choose any format connector RJ45 and
maybe add PoE then. And are halt the price The eeprom is mandatory in order to ESC read save some internal configuration. Leds are optional, but the PHY's has som pins used as a boostrap, so you

have to respet that

the pullup of led_0 is mandatory, but to
drive the led you could choose between PHY or uC populating/unpopulating the jumper

Led- 20 Led+ TD+ Led- 22 Led- 16 Led+ TD- 3 RD+ Led- 18 shield shield

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

2k2 pullup as
indicated by phy IC's

P1_RD_P
P1_RD_N

RX_DV/MII_MODE 26
RX_ER/AMDIX_EN 28
RX_CLK 25
RX_D0/PHYAD1 30
RX_D2/PHYAD3 32

ecat1_col ecat1_crs | COL/PHYAD0/MLED 29

Run and Error LEDs

It's a good idea to have them on
these fitst stage but could be

Id: 4/20 Title: ethercat File: ethercat.sch Sheet: /ethercat/ dci Pablo Slavkin

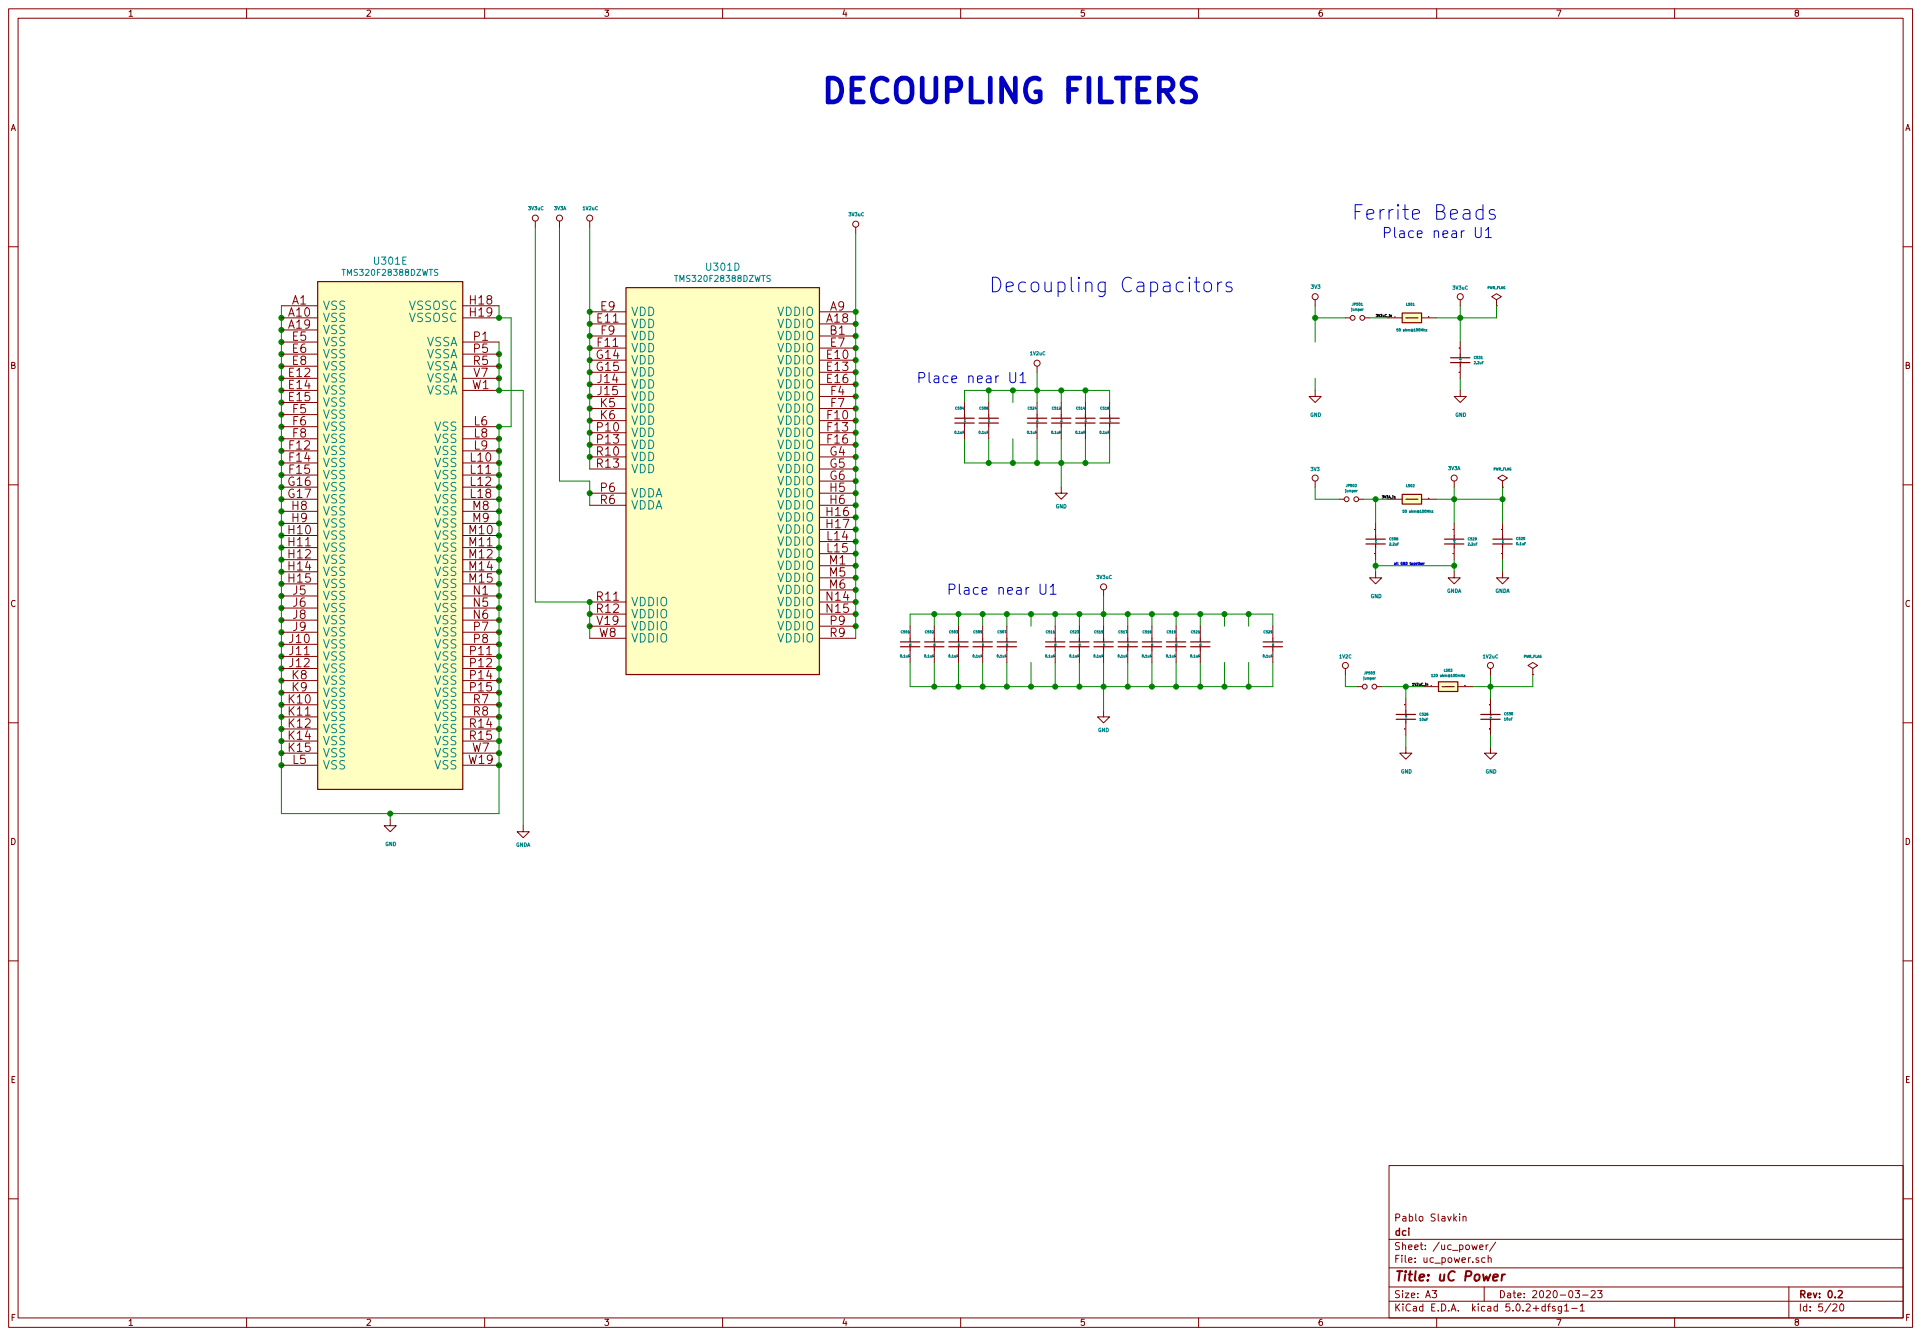
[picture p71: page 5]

VSS E12
VSS E14

1 Capacitor 2 C529
all GND together GND

Sheet: /uc_power/ dci Pablo Slavkin Place near U1

VSS K8
VSS K9

File: uc_power.sch
Id: 5/20 Title: uC Power

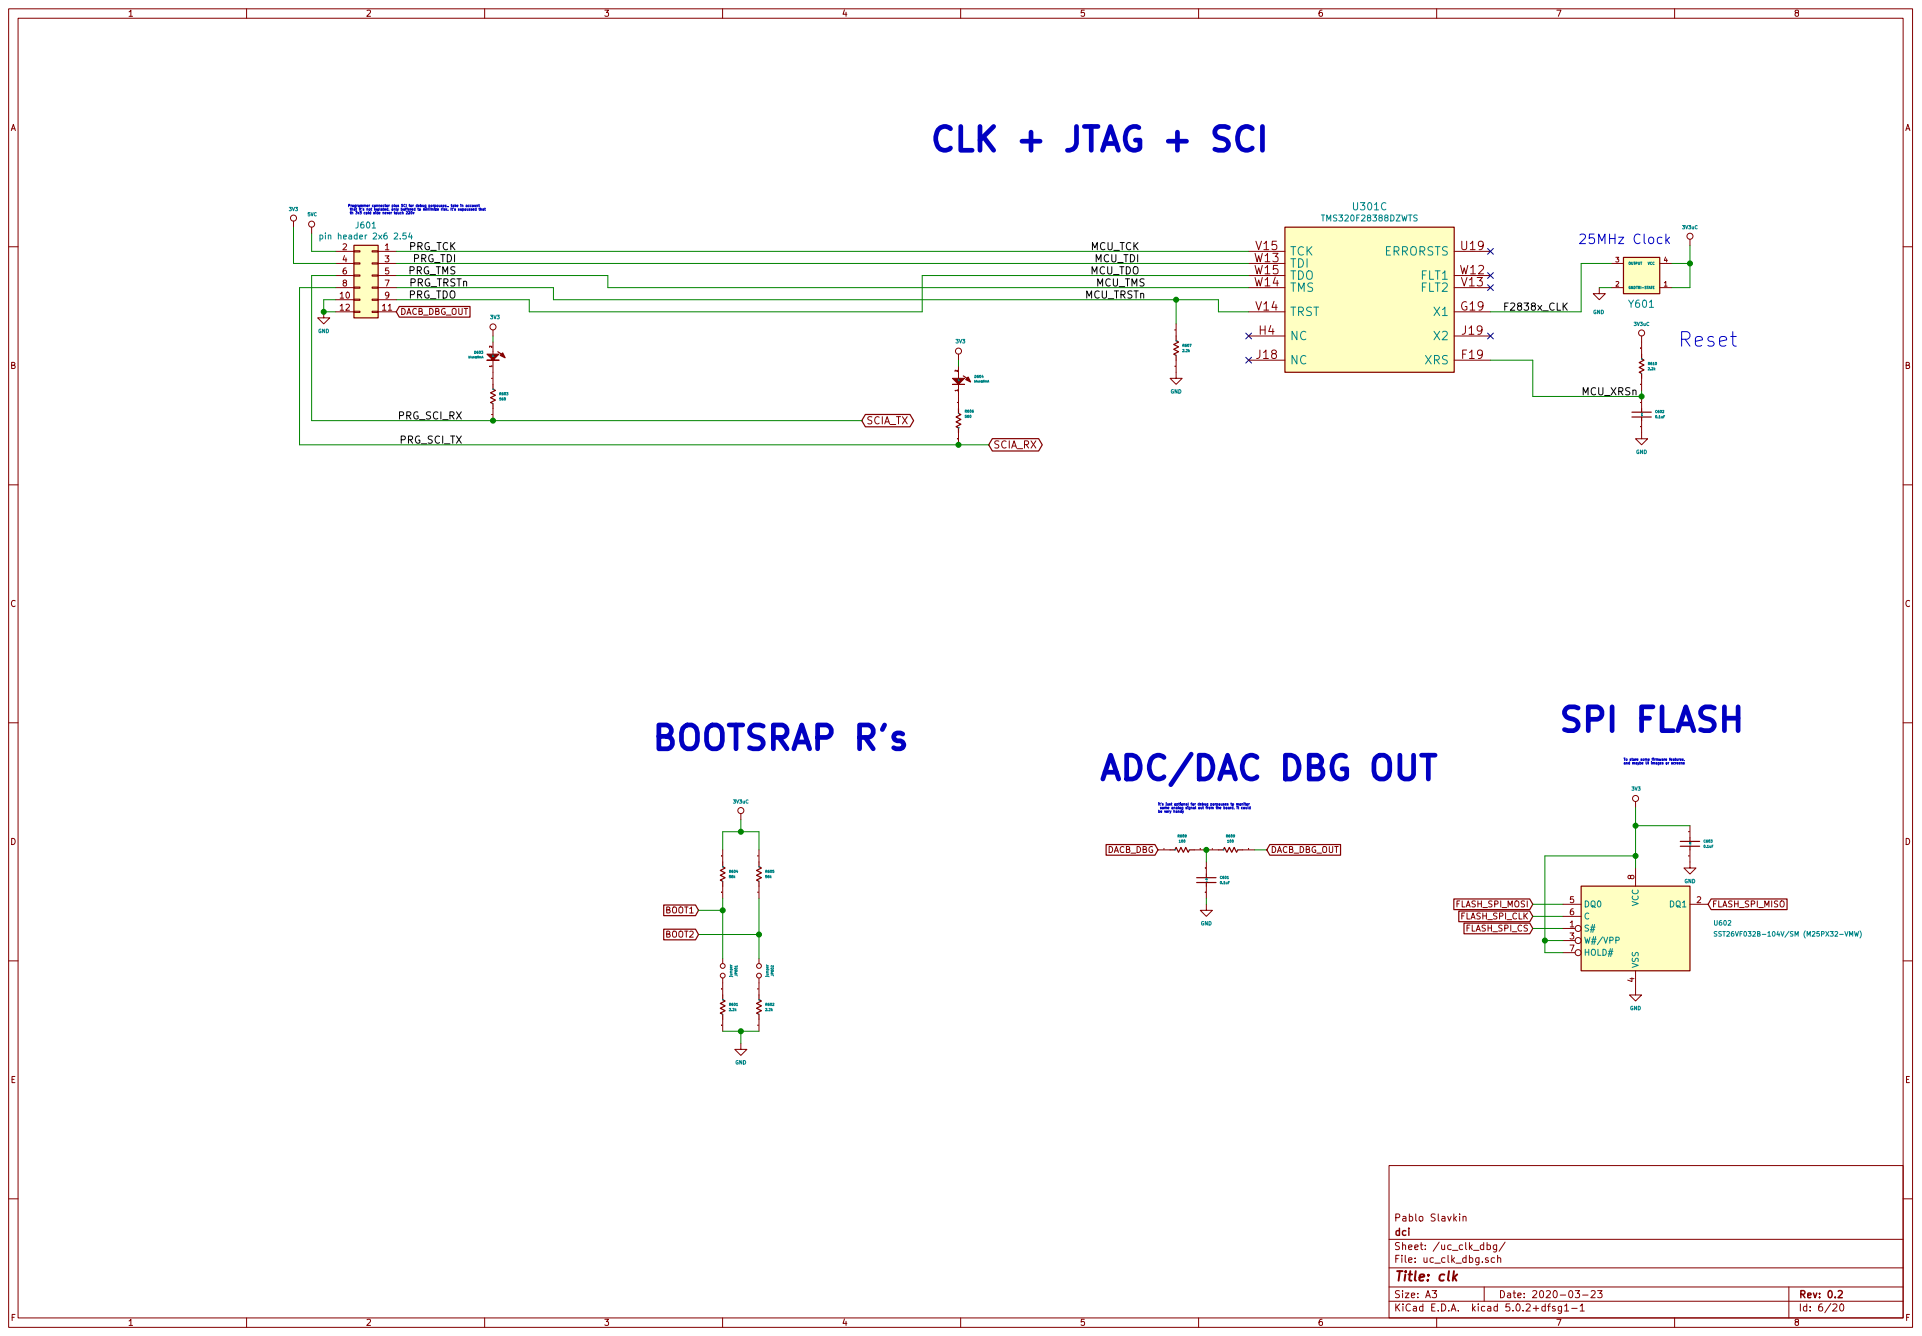
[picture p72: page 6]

Programmer connector plus SCI for debug porpouses.. take in account
that it's not isolated, only buffered to minimize risk. It's supoussed that
pin header 2x6 2.54

some analog signal out from the board, it could be very handy PRG_SCI_RX

8 U602SST26VF032B-104V/SM (M25PX32-VMW) SPI FLASH

100 GND ADC/DAC DBG OUT

To store some firmware features, and maybe UI images or screens

it's just optional for debug porpouses to monitor

Sheet: /uc_clk_dbg/ dci Pablo Slavkin

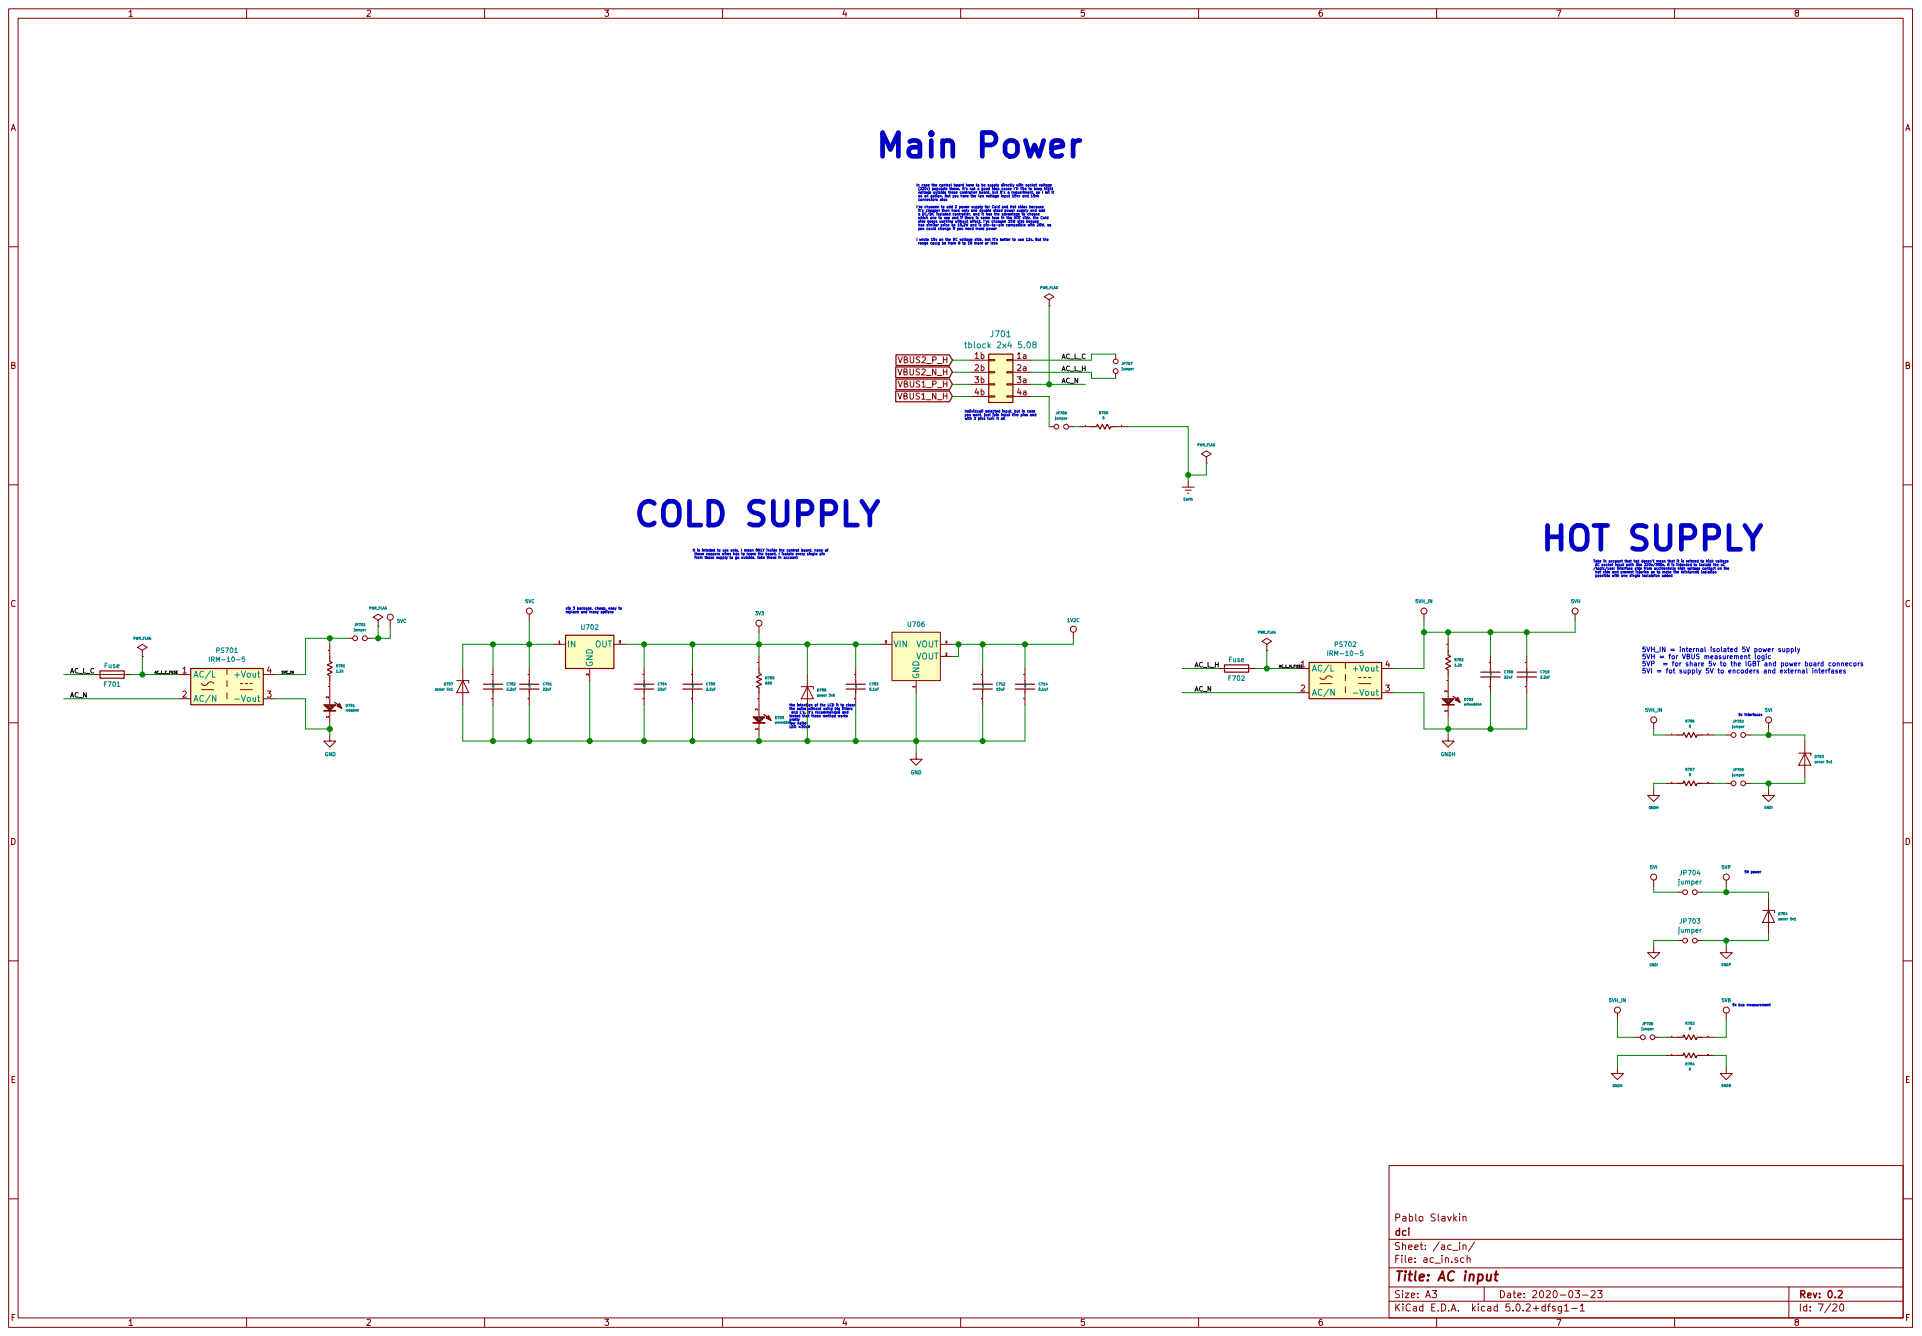
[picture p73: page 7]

In case the control board have to be supply directly with socket voltage
(220v) populate these. It's not a good idea cause I'll like to keep hight
voltage outside these controller board, but it's a requeriment, so I let it
as an option. But you have the low voltage input 15vc and 15vh
connectors also
I've choosen to add 2 power supply for Cold and Hot sides because
it's cheaper than have only one double sized power supply and add
a DC/DC isolated controller, and it has the advantage to choose
which one to use and if there is some isue in the HOT side, the Cold
side keeps working without affect. I've choosen 15W size beouse
has similar price as 10.2W and is pin-to-pin compatible with 20W, so
you could change if you need more power

I wrote 15v on the DC voltage side, but it's better to use 12v. But the
range coulg be from 8 to 18 more or less

It is inteded to use only, I mean ONLY inside the control board, none of
these coopers wires has to leave the board. I isolate every single pin
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

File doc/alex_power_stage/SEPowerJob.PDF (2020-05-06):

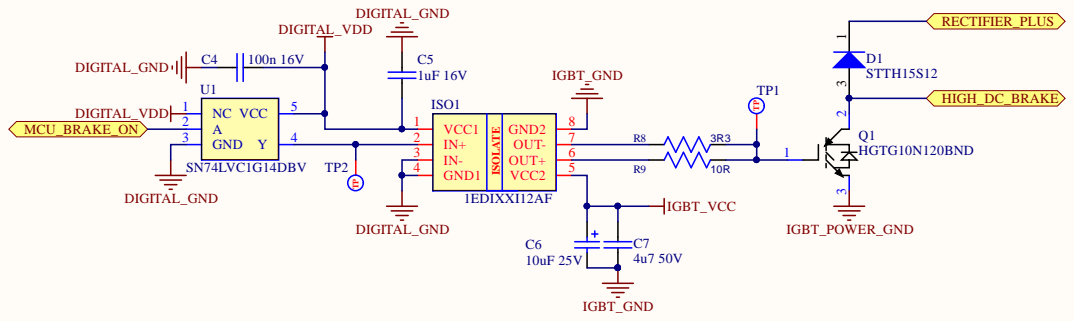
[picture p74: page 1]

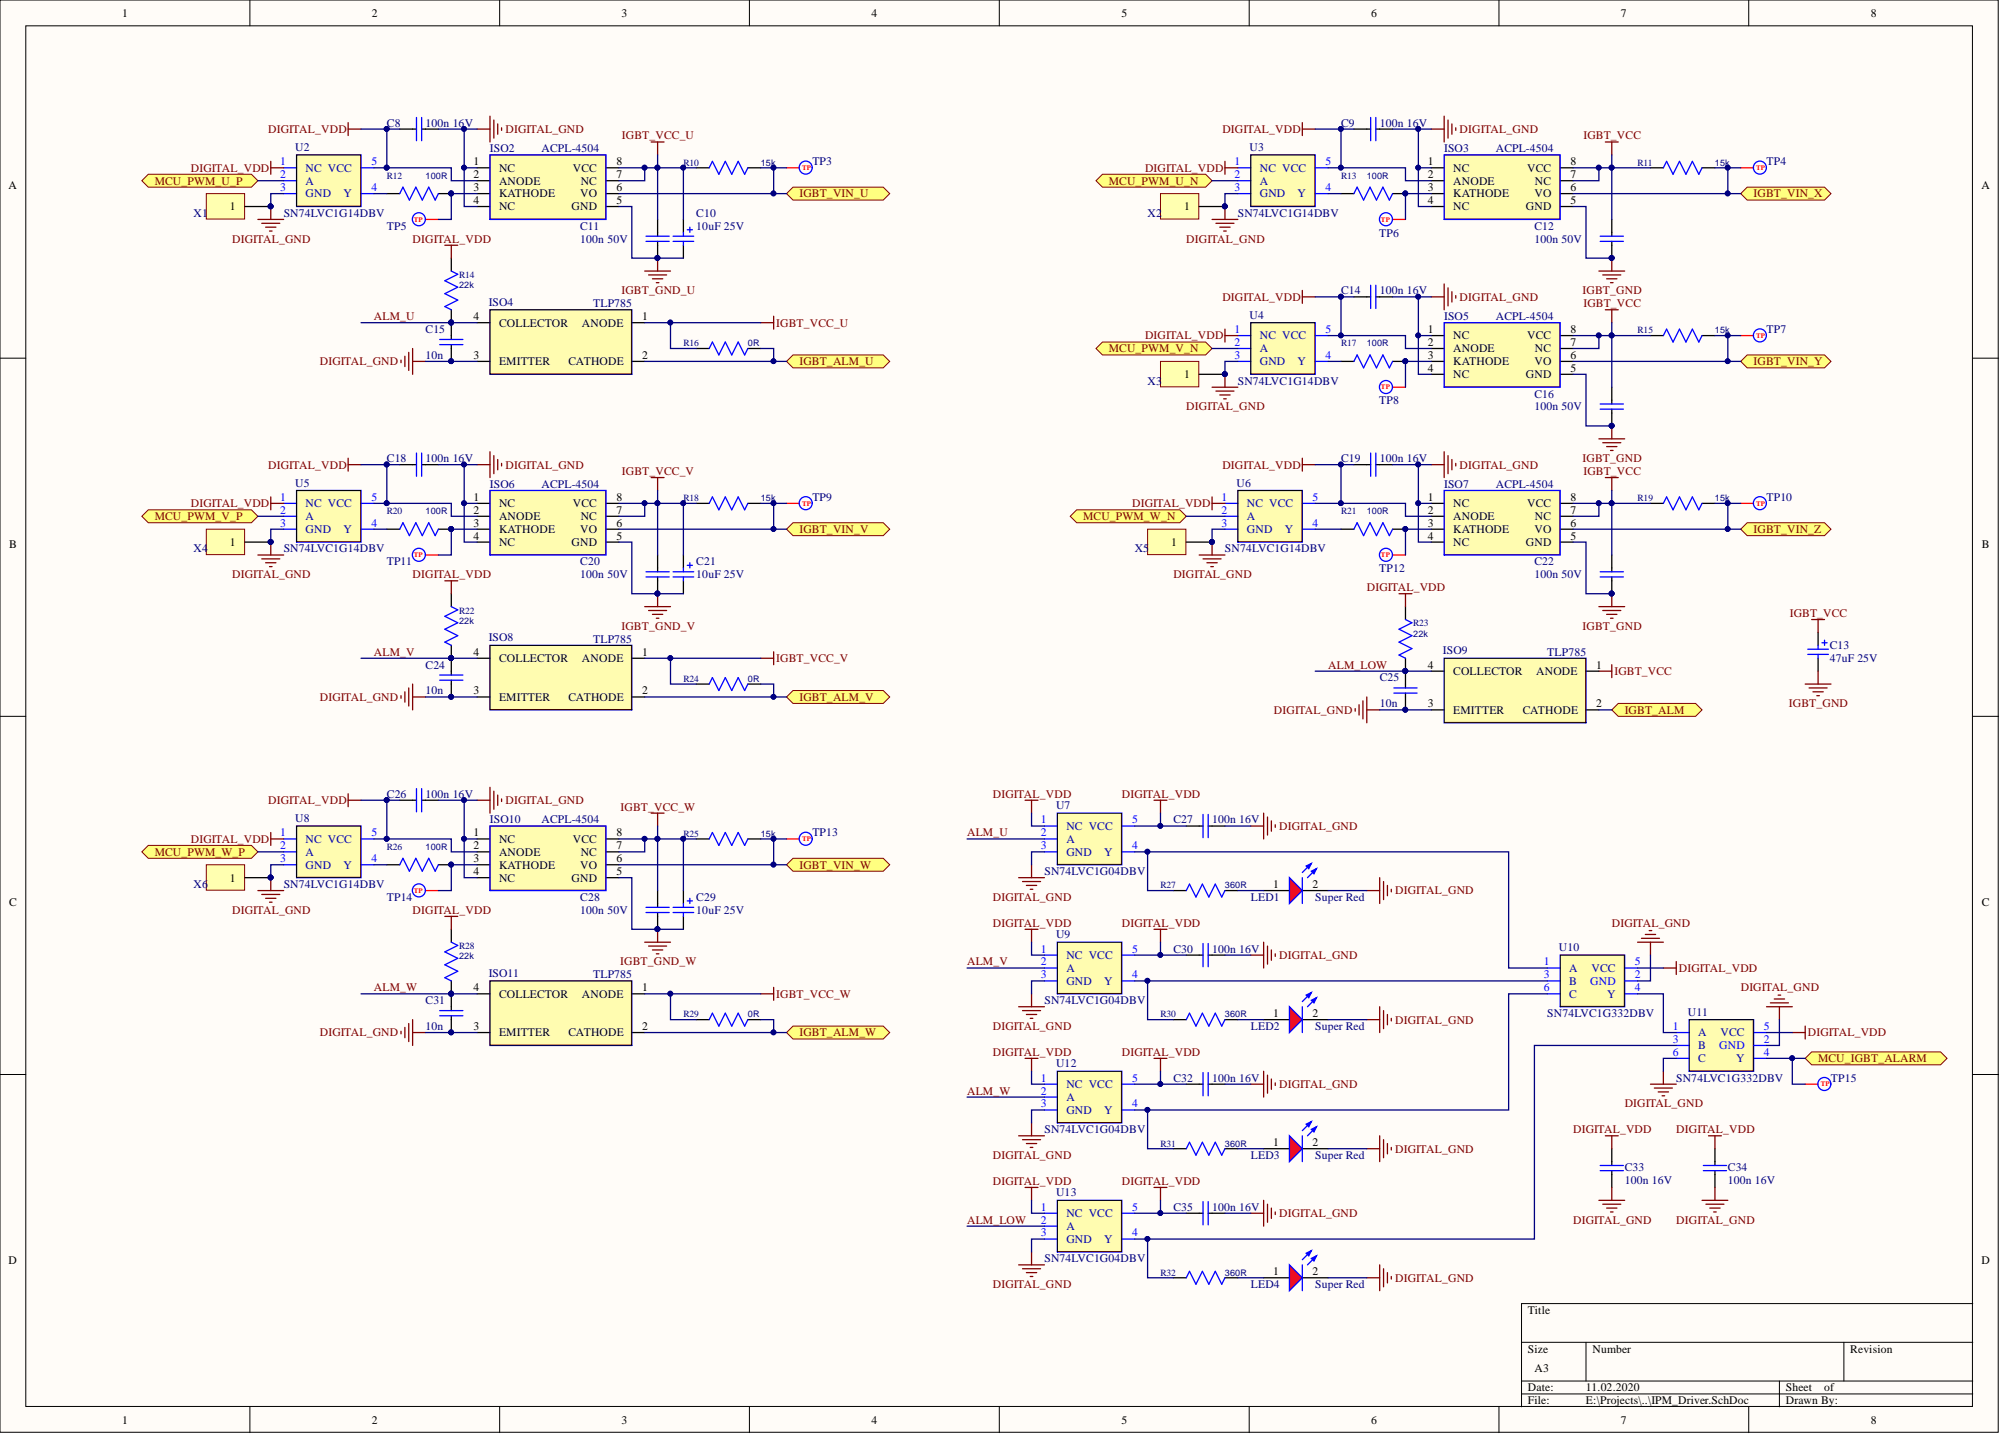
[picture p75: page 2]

A 2 | R17 100R | ANODE 2

KATHODE 3

A 2 | R26 100R | ANODE 2

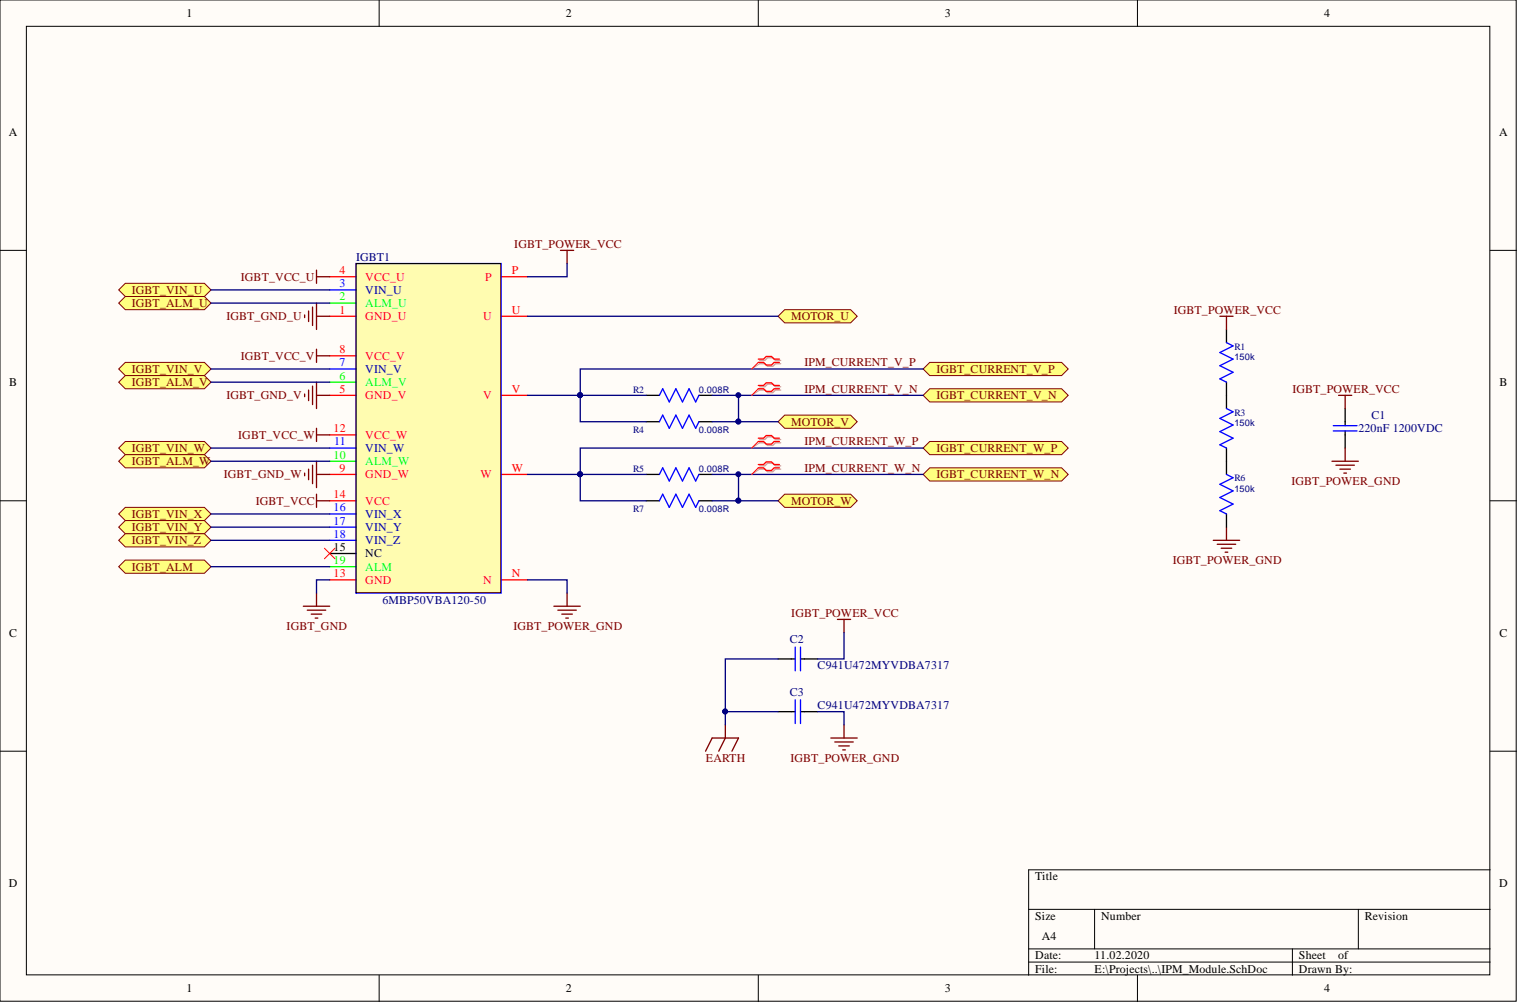
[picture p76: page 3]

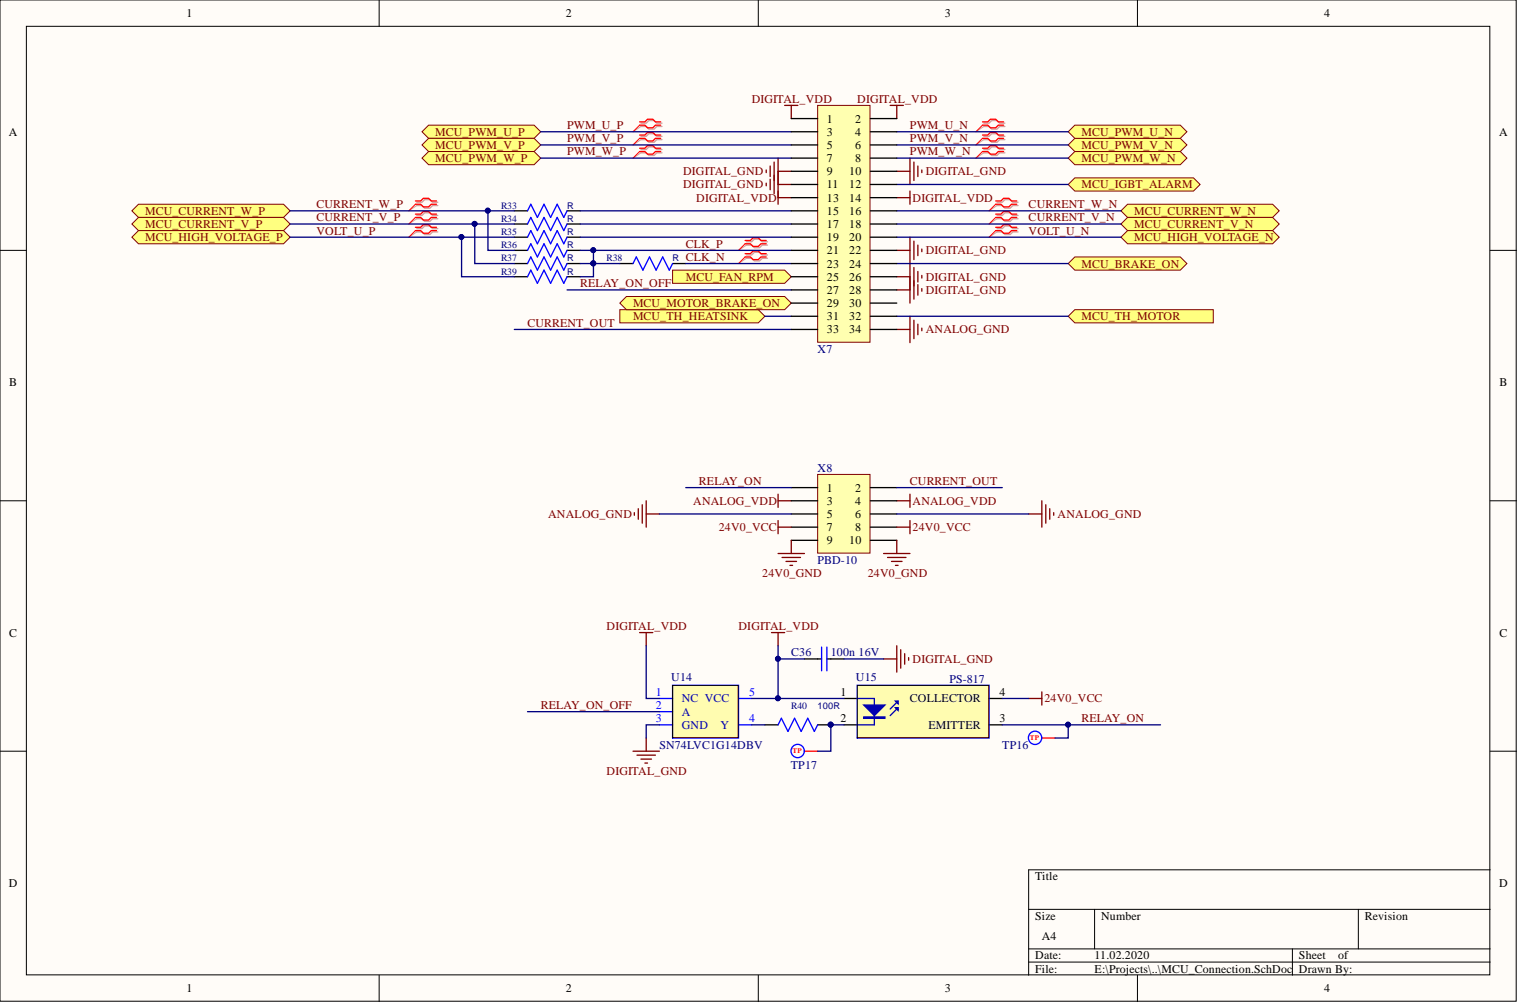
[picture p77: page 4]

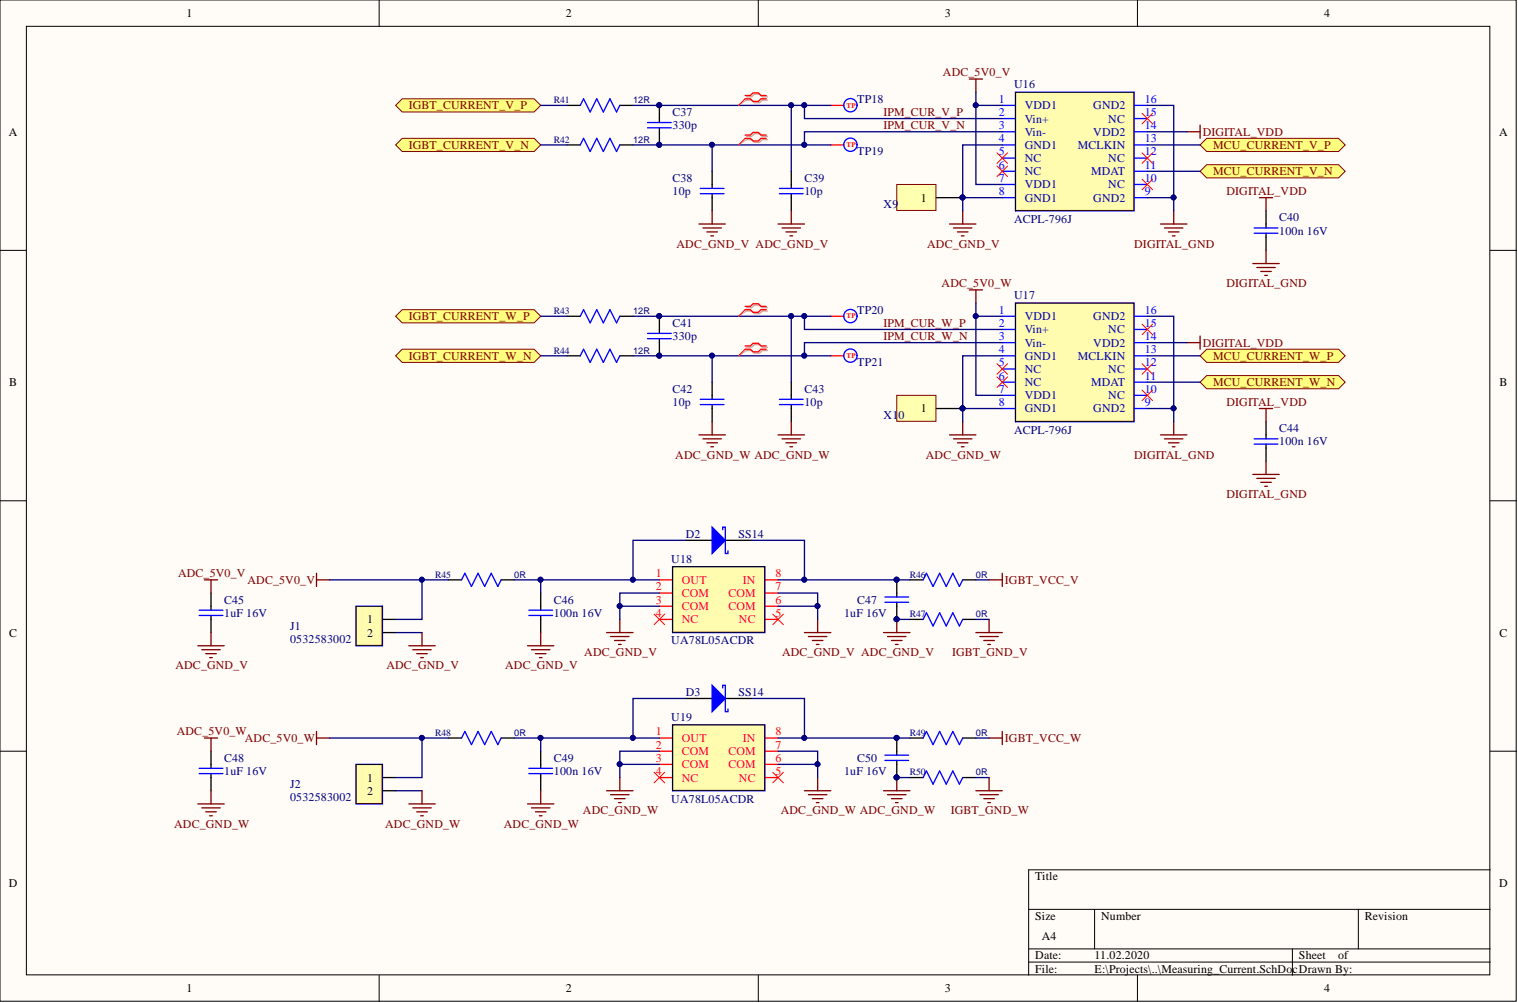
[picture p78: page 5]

OUT 1 COM 2

COM 3


Heat sink external thermal resistor

internal motor thermal resistor

FAN_VCC
FAN_GND


GND1 4







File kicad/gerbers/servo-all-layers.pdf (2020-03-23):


F Date: 2020-03-03 KiCad E.D.A. kicad 5.0.2+dfsg1-1 Rev: 1.0 Size: A3

Id: 1/1 Pablo Slavkin DCI nanocut Sheet: File: servo.kicad_pcb

Title: Servo Drive

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

Id: 1/1 Pablo Slavkin DCI nanocut Sheet: File: servo.kicad_pcb

Title: Servo Drive

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

Id: 1/1 Pablo Slavkin DCI nanocut Sheet: File: servo.kicad_pcb

Title: Servo Drive

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

Id: 1/1 Pablo Slavkin DCI nanocut Sheet: File: servo.kicad_pcb

+VBUS1- +VBUS2- EARTH N LH LC AC IB_U IB_ALL IB_V IA_ALL IA_V IA_U C526 JP708 R708 Servo Controller

1 2 3 4 5 6 7 8

1 2 3 4 5 6 7 8 A

F A

# F Date: 2020-03-03 KiCad E.D.A. kicad 5.0.2+dfsg1-1 Rev: 1.0 Size: A3

# Id: 1/1 Pablo Slavkin DCI nanocut Sheet: File: servo.kicad_pcb

# Title: Servo Drive

# PnP origin 150.000 mm

160.000 mm

# silkscreen bottom color +- 0.05 mm

+- 0.05 mm

# min via drill 0.0953 mm

# min track width

holes registration tolerance holes size tolerance min track to track clrearance min via diameter metal registration tolerance PTH copper thickness

# silkscreen top color solder resist color board thickness notes

# information

0.457 mm

# 0.3 mm

+- 0.05 mm

# 20 to 30 um

# white white blue semi gloss FR-4 High Tg board material 0.1524 mm

# 1.6 mm

# 18 mils

# 6 mils

# 6 mils min track to pad clearance

0.1524 mm

# min pad to pad clearance 0.1238 mm

# 3.7 mils

# 4.8 mils

# 12 mils but it has smaller clearance ONLY near BGA on circle pad to circle

the intention of the board is to fit on 6mils/6mils standard pad and circle pad to track clearance.If it obey to change the standard

# I'd change thouse reducing drill holes to 0.2

23

24

# footprint position top

# footprint position bottom

# Cmts.User.gbr

# top.pos bottom.pos

# 22 board information

18

19

20

# 21 PTH.drl NPTH.drl Dwgs.User.gbr NPTH holes

# slotted holes Edge.Cuts.gbr

# top adhesive F.Adhes.gbr F.Paste.gbr top paste F.SilkS.gbr F.Mask.gbr F.Cu.gbr GND.Cu.gbr

# In3.Cu.gbr

# In4.Cu.gbr VCC.Cu.gbr B.Cu.gbr B.Mask.gbr B.SilkS.gbr

# file name [*-] 17 PTH holes board edge cuts

16

# top silskscreen

# top solder mask

# top copper dielectric 1

# internal plane 2 dielectric 2

# signal layer 3 dielectric 3

# signal layer 4 dielectric 4

# internal plane 5 bottom cooper bottom solder mask bottom silkscreen

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
# 14 Layer Function Material Thickness

# solder resist cooper FR-4

# cooper FR-4

# cooper FR-4

# cooper FR-4

# cooper FR-4 dielectric 5

# 15 cooper white tint solder resist white tint 20 um

# 35 um

# 35 um

# 35 um

# 35 um

# 35 um

# 35 um

# 20 um STACKUP

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

Id: 1/1 Pablo Slavkin DCI nanocut Sheet: File: servo.kicad_pcb

Title: Servo Drive

these sloted holes on Dwgs.User

layer are NPTH milled holes 0.8mm width

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

Id: 1/1 Pablo Slavkin DCI nanocut Sheet: File: servo.kicad_pcb

Title: Servo Drive

ECAT0 ECAT1

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

Id: 1/1 Pablo Slavkin DCI nanocut Sheet: File: servo.kicad_pcb

Title: Servo Drive

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

Id: 1/1 Pablo Slavkin DCI nanocut Sheet: File: servo.kicad_pcb

Title: Servo Drive

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

Id: 1/1 Pablo Slavkin DCI nanocut Sheet: File: servo.kicad_pcb

Title: Servo Drive

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

Id: 1/1 Pablo Slavkin DCI nanocut Sheet: File: servo.kicad_pcb

+RS485- GNDI 5VI +CAN- +DATA- +CLK- 5VI GNDI GNDI +QEPS- +QEPI- +QEPB- +QEPA- 5VI GNDI 5VI +DIR- +STEP-

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

Id: 1/1 Pablo Slavkin DCI nanocut Sheet: File: servo.kicad_pcb

Title: Servo Drive

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

Id: 1/1 Pablo Slavkin DCI nanocut Sheet: File: servo.kicad_pcb

Title: Servo Drive
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



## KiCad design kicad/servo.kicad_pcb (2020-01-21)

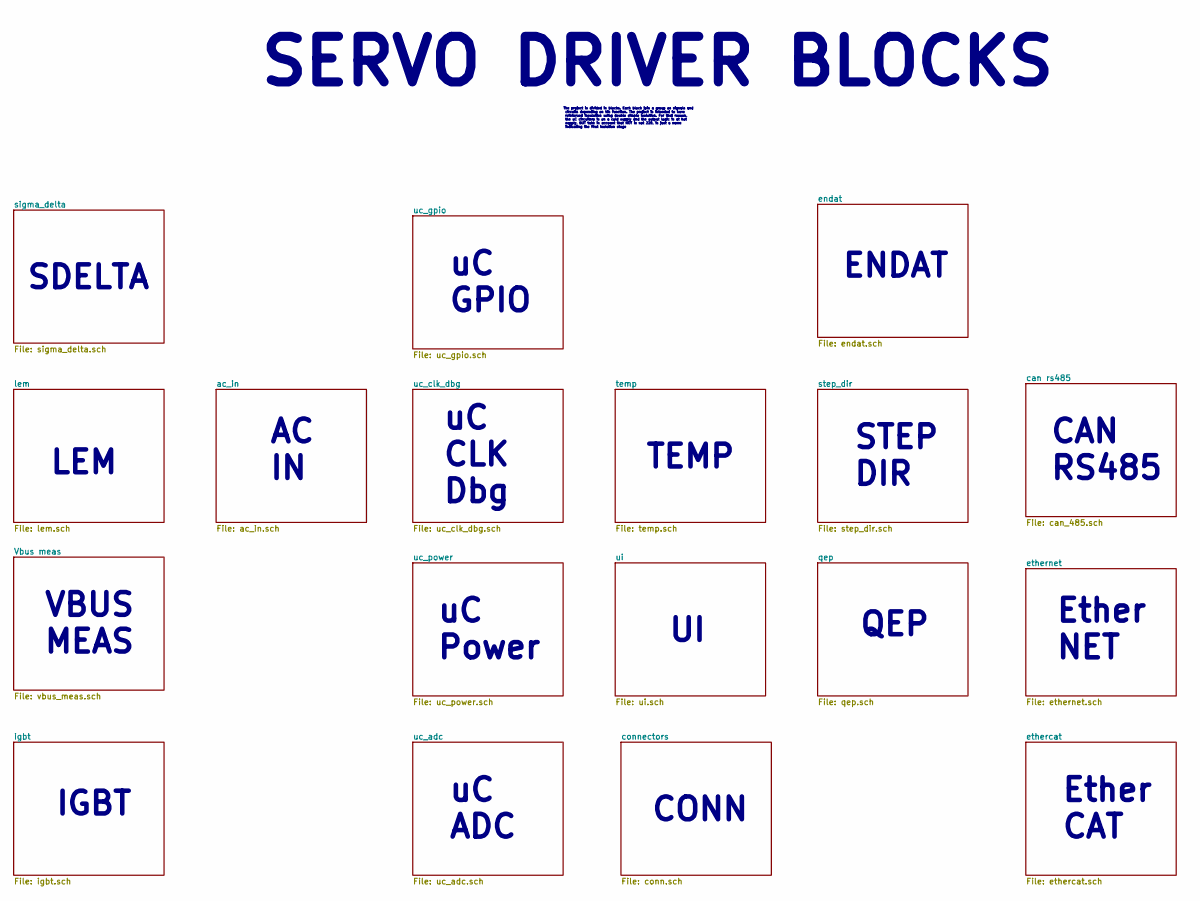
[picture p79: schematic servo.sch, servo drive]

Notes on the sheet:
uC ADC
IGBT
uC Power
Ether CAT
TEMP
AC IN
Ether NET
uC CLK Dbg
STEP DIR
QEP
CAN RS485
uC GPIO
LEM
VBUS MEAS
CONN
SERVO DRIVER BLOCKS
The project is divided in blocks. Each block join a group os signals and circuits depending on his function. The project is intended to have reinforced insulation using double simple isolation. For that reason, the uC circuitery is on a cold supply and the output logic is at hot supply, BUT take in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
SDELTA
ENDAT

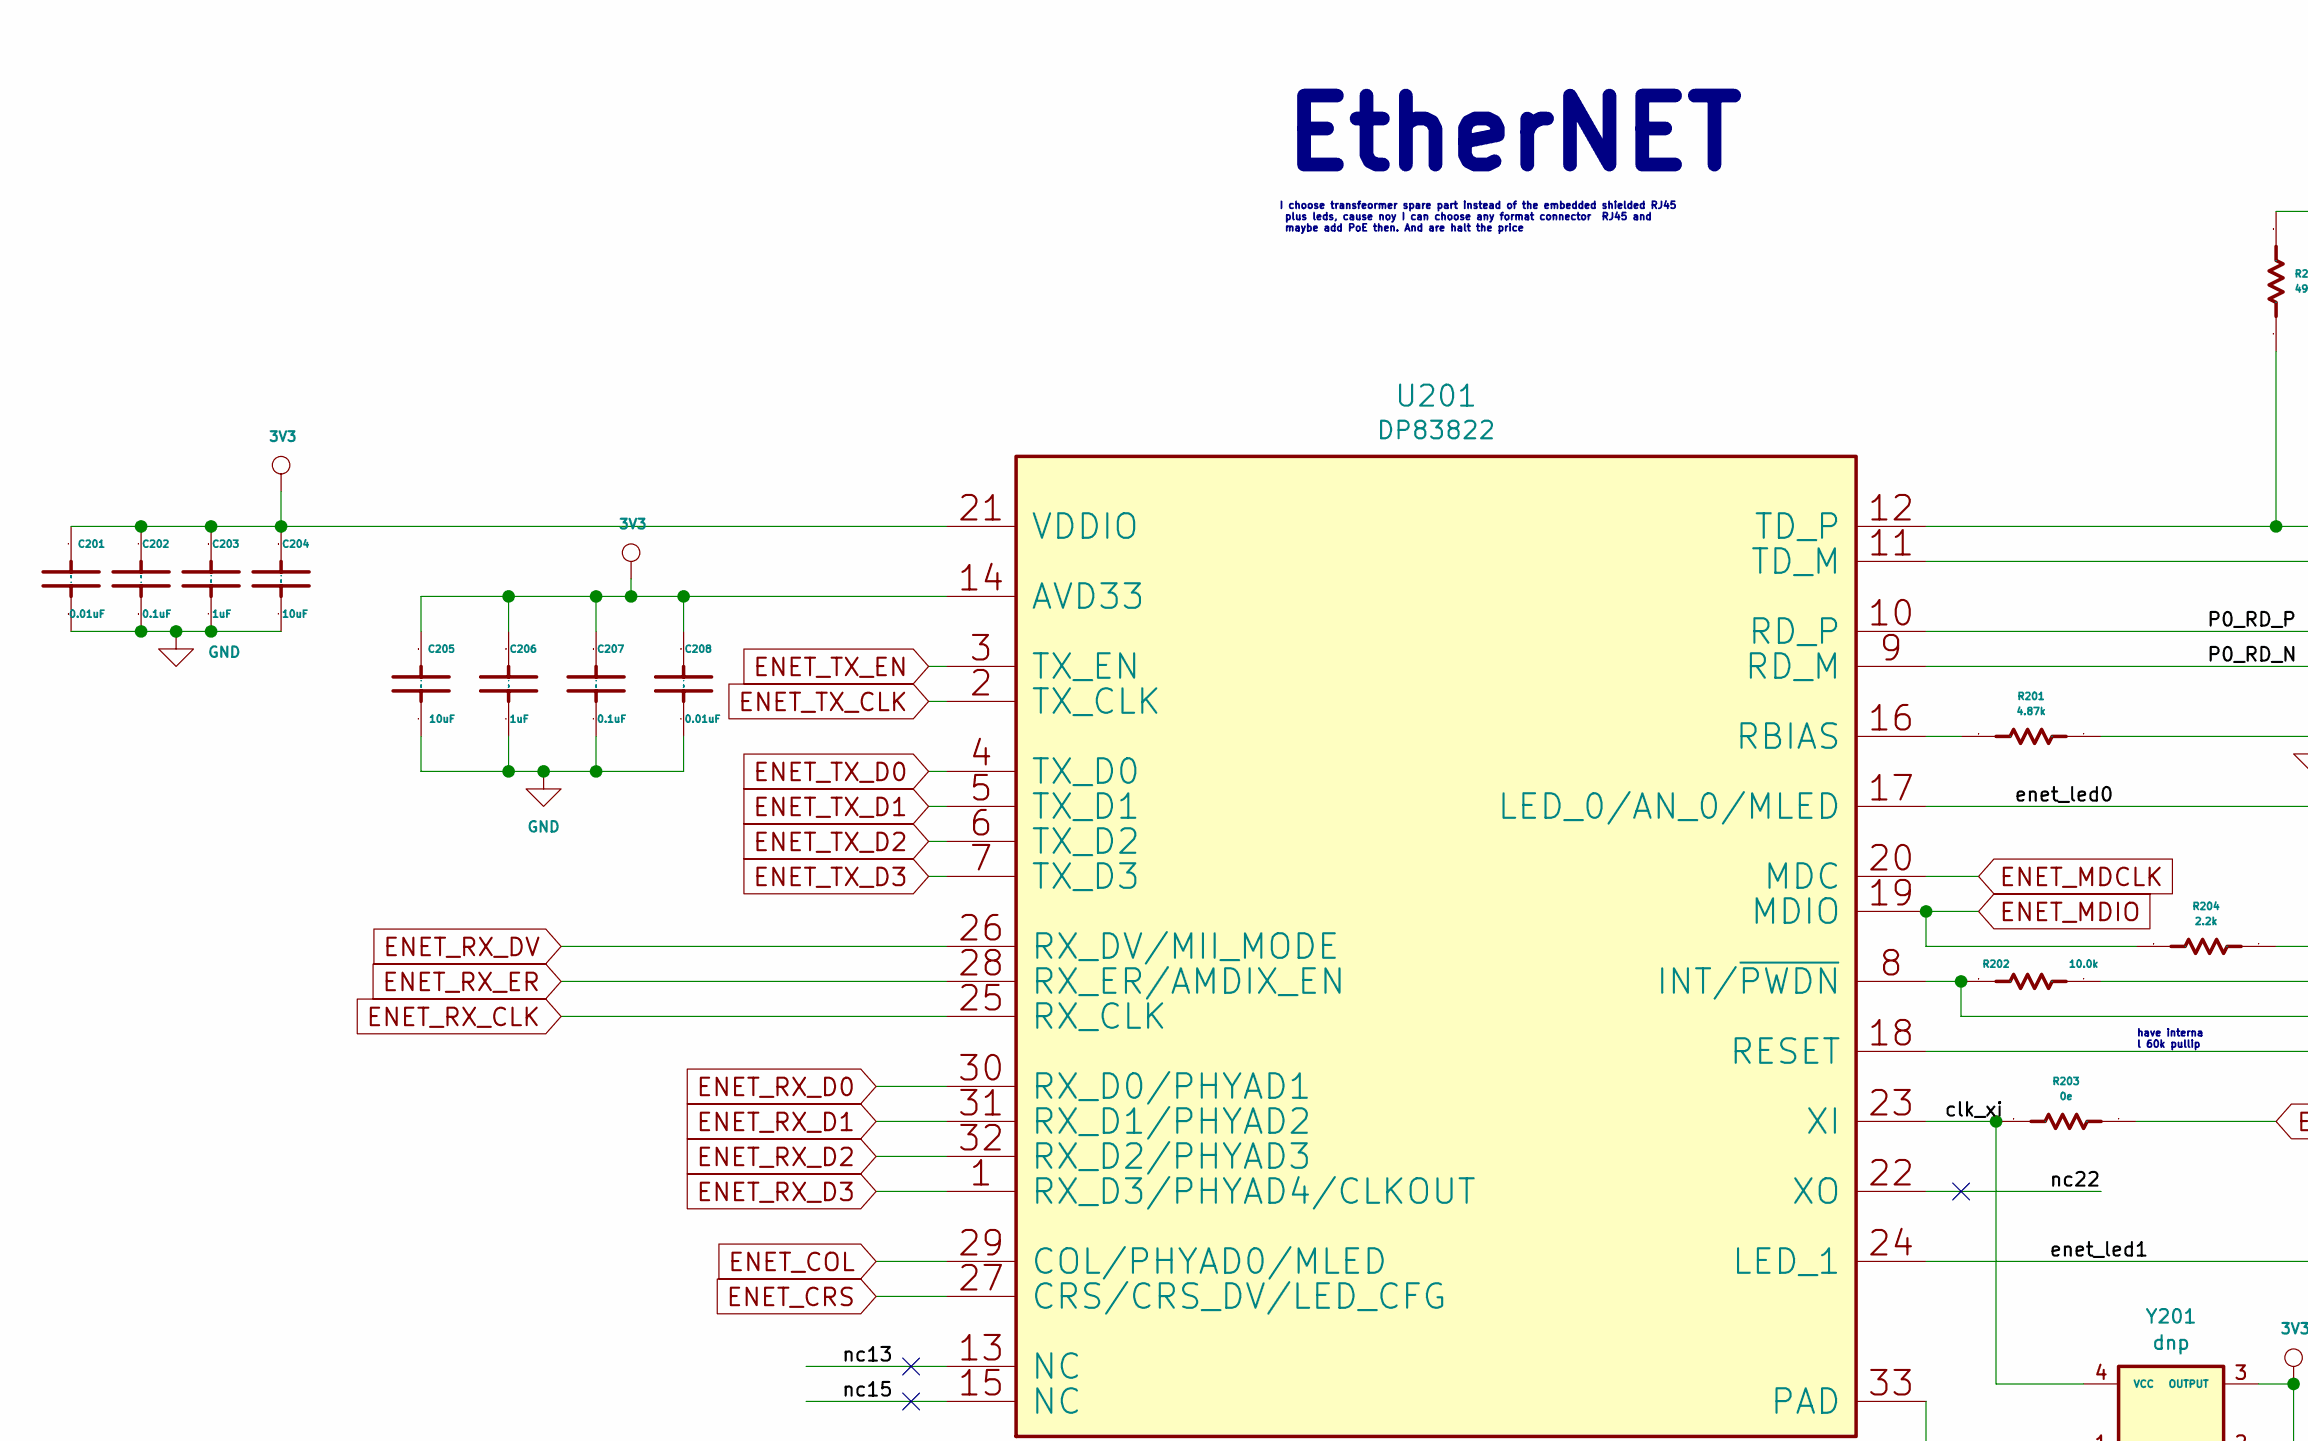
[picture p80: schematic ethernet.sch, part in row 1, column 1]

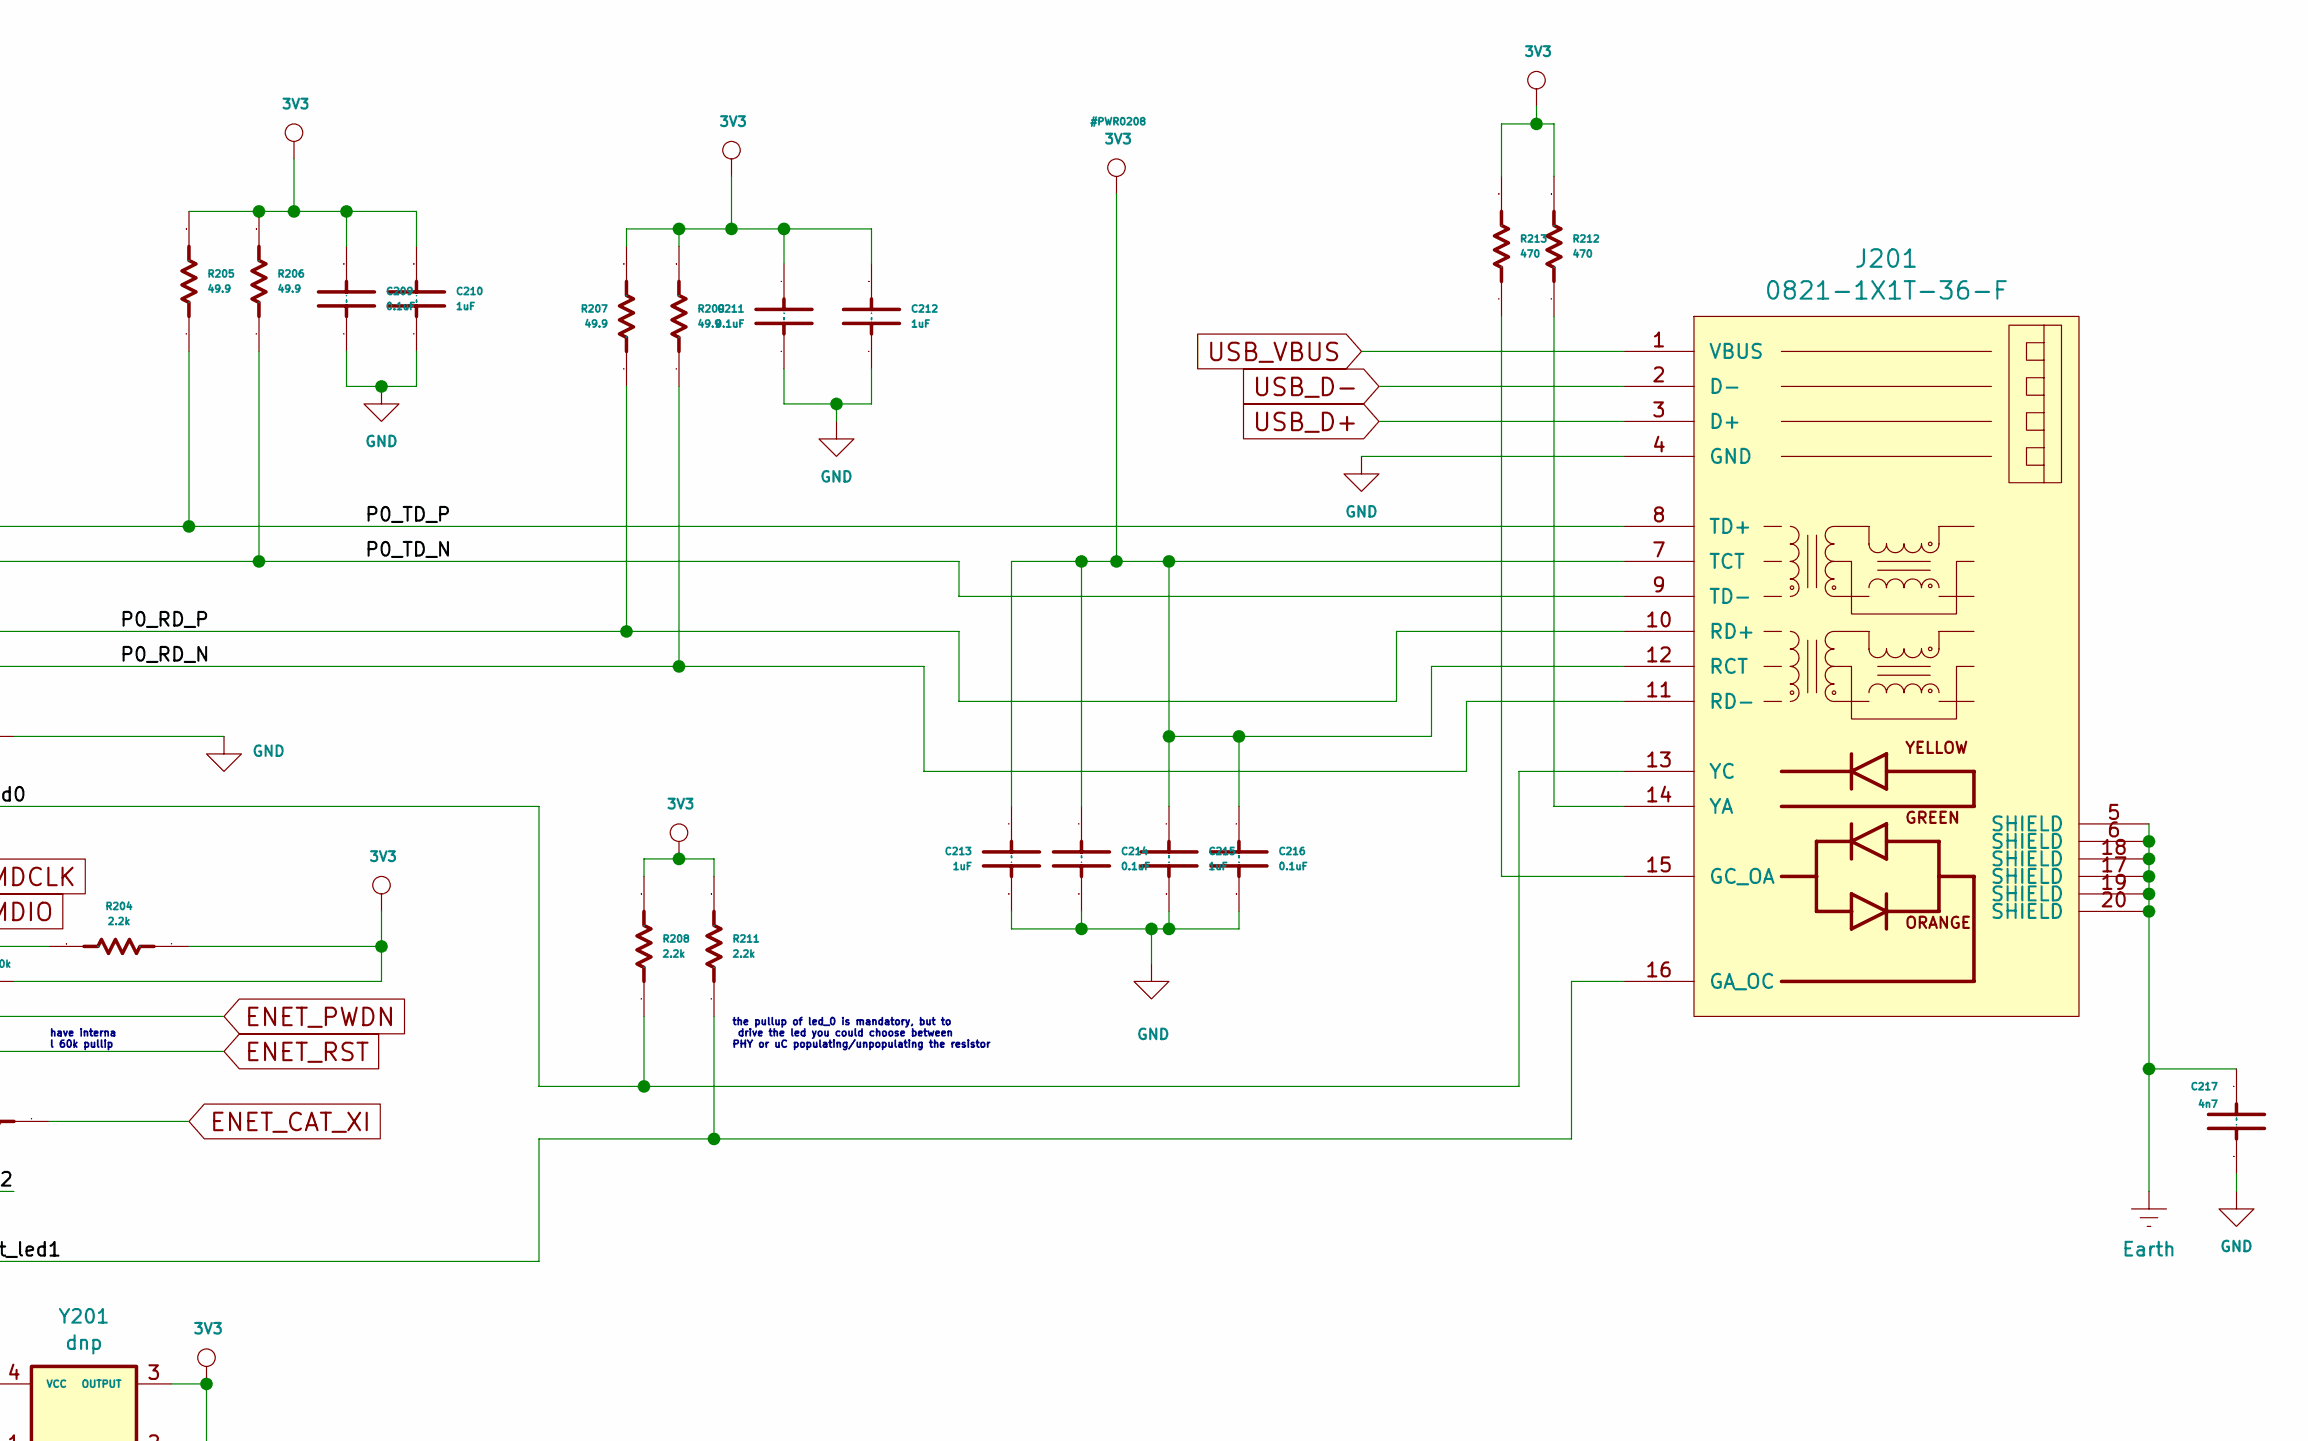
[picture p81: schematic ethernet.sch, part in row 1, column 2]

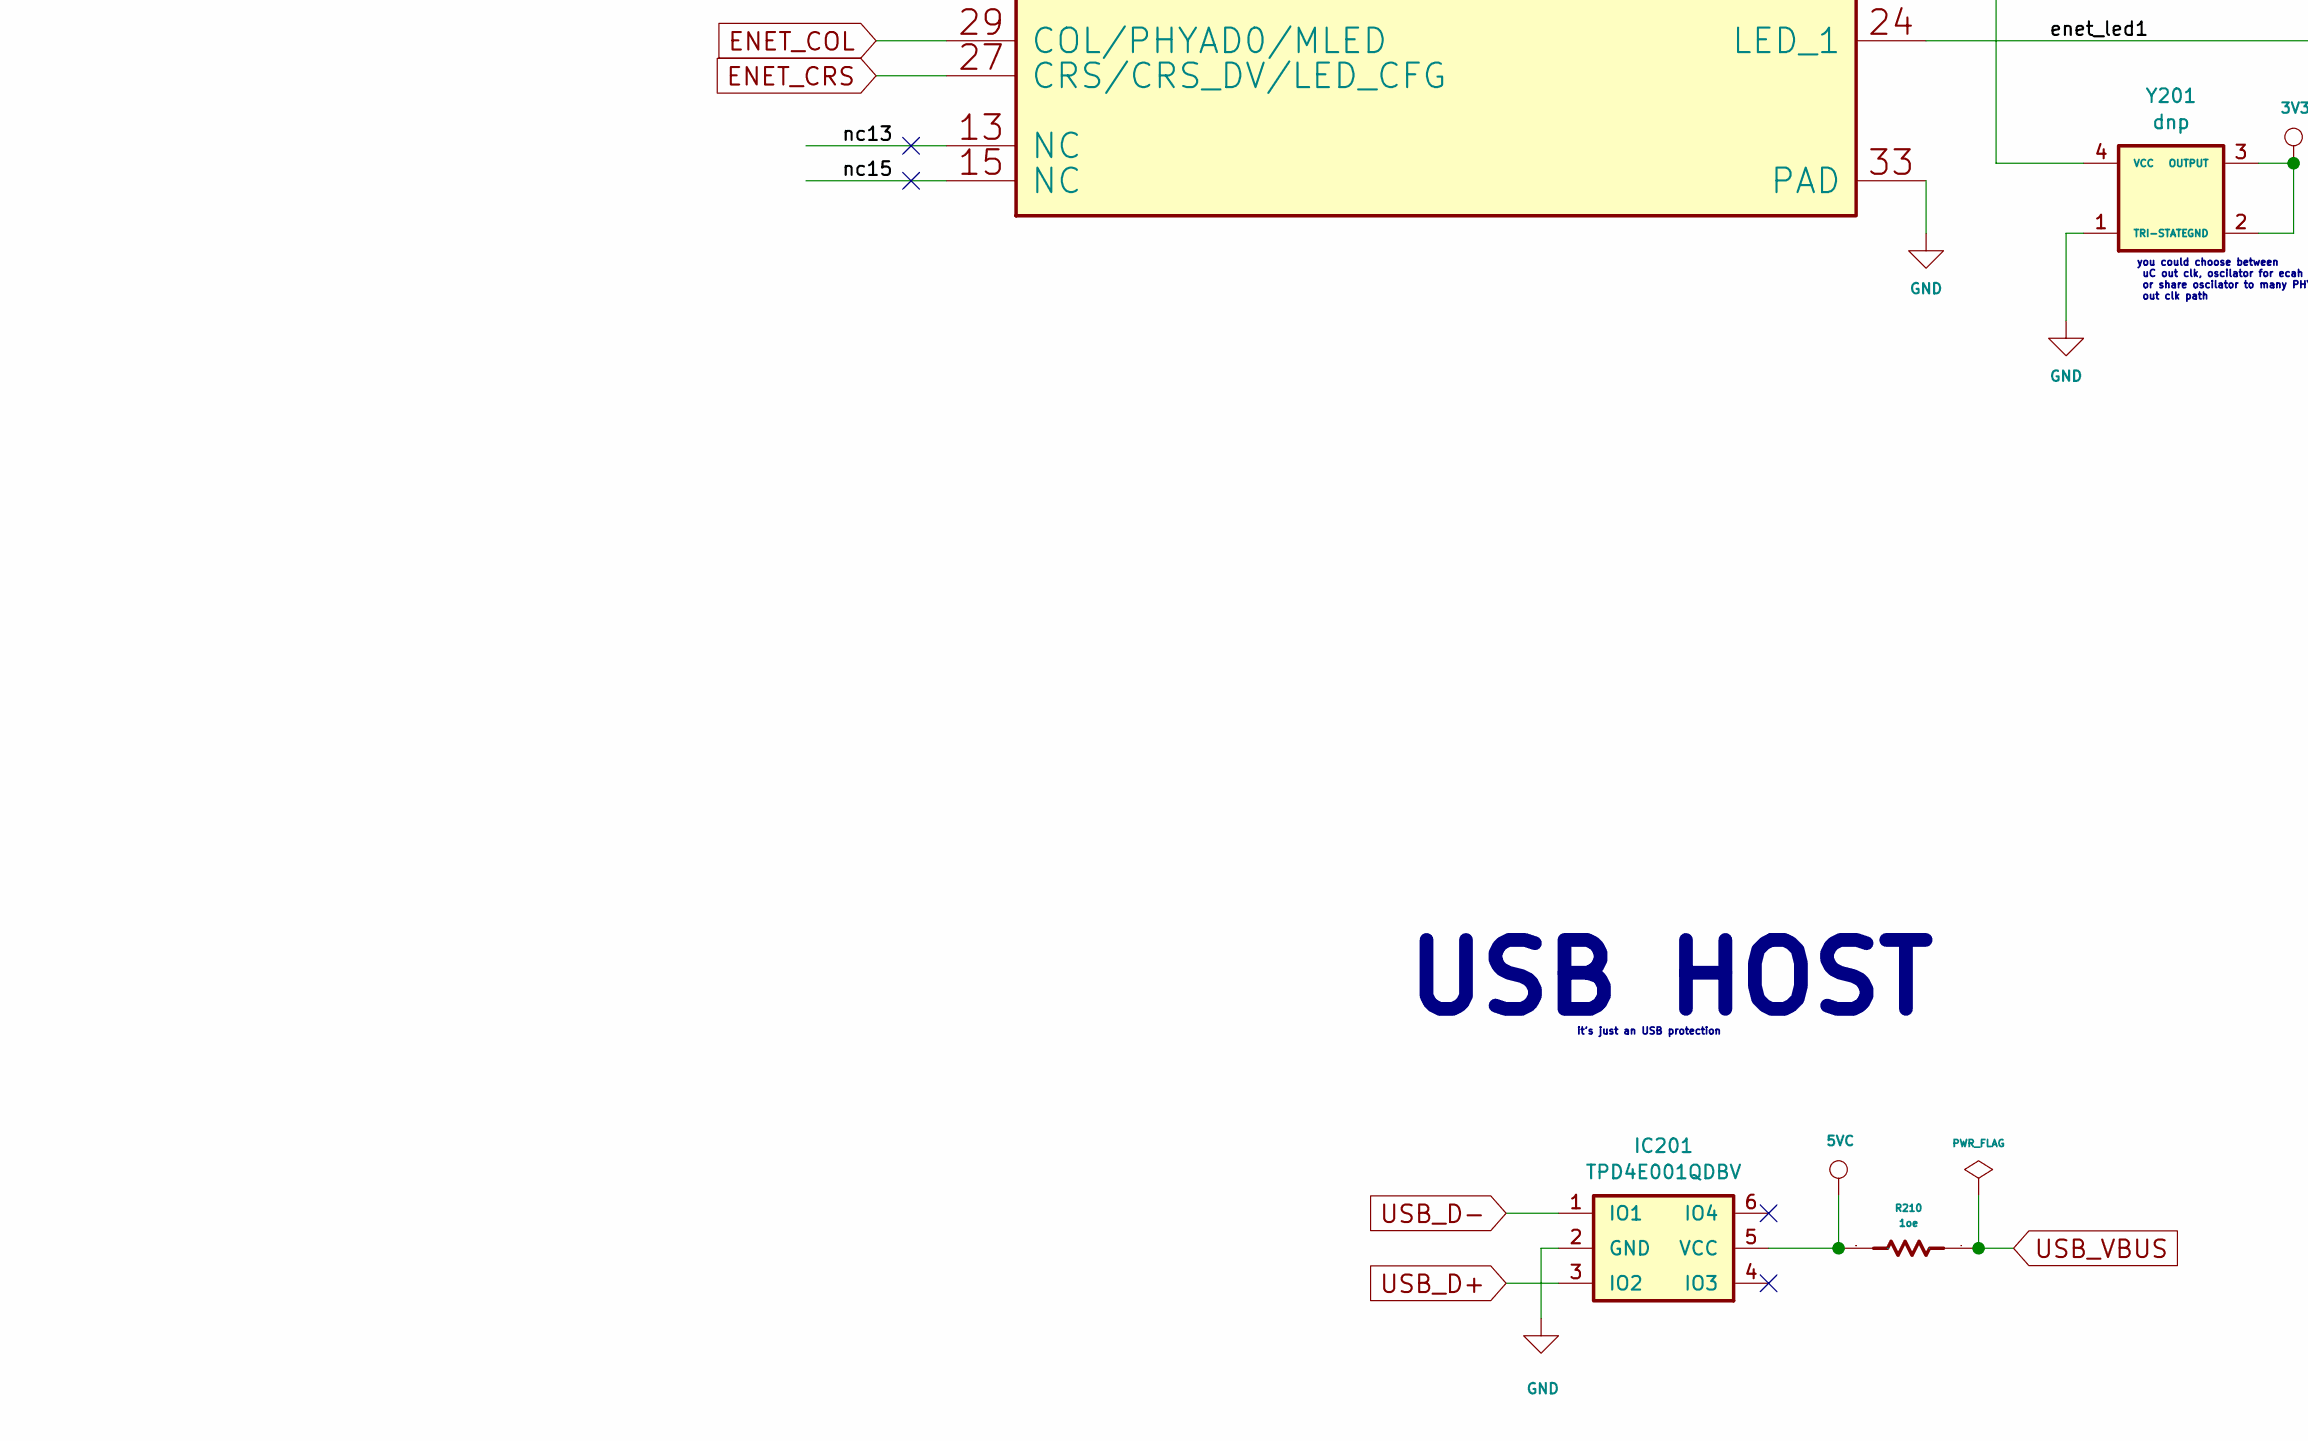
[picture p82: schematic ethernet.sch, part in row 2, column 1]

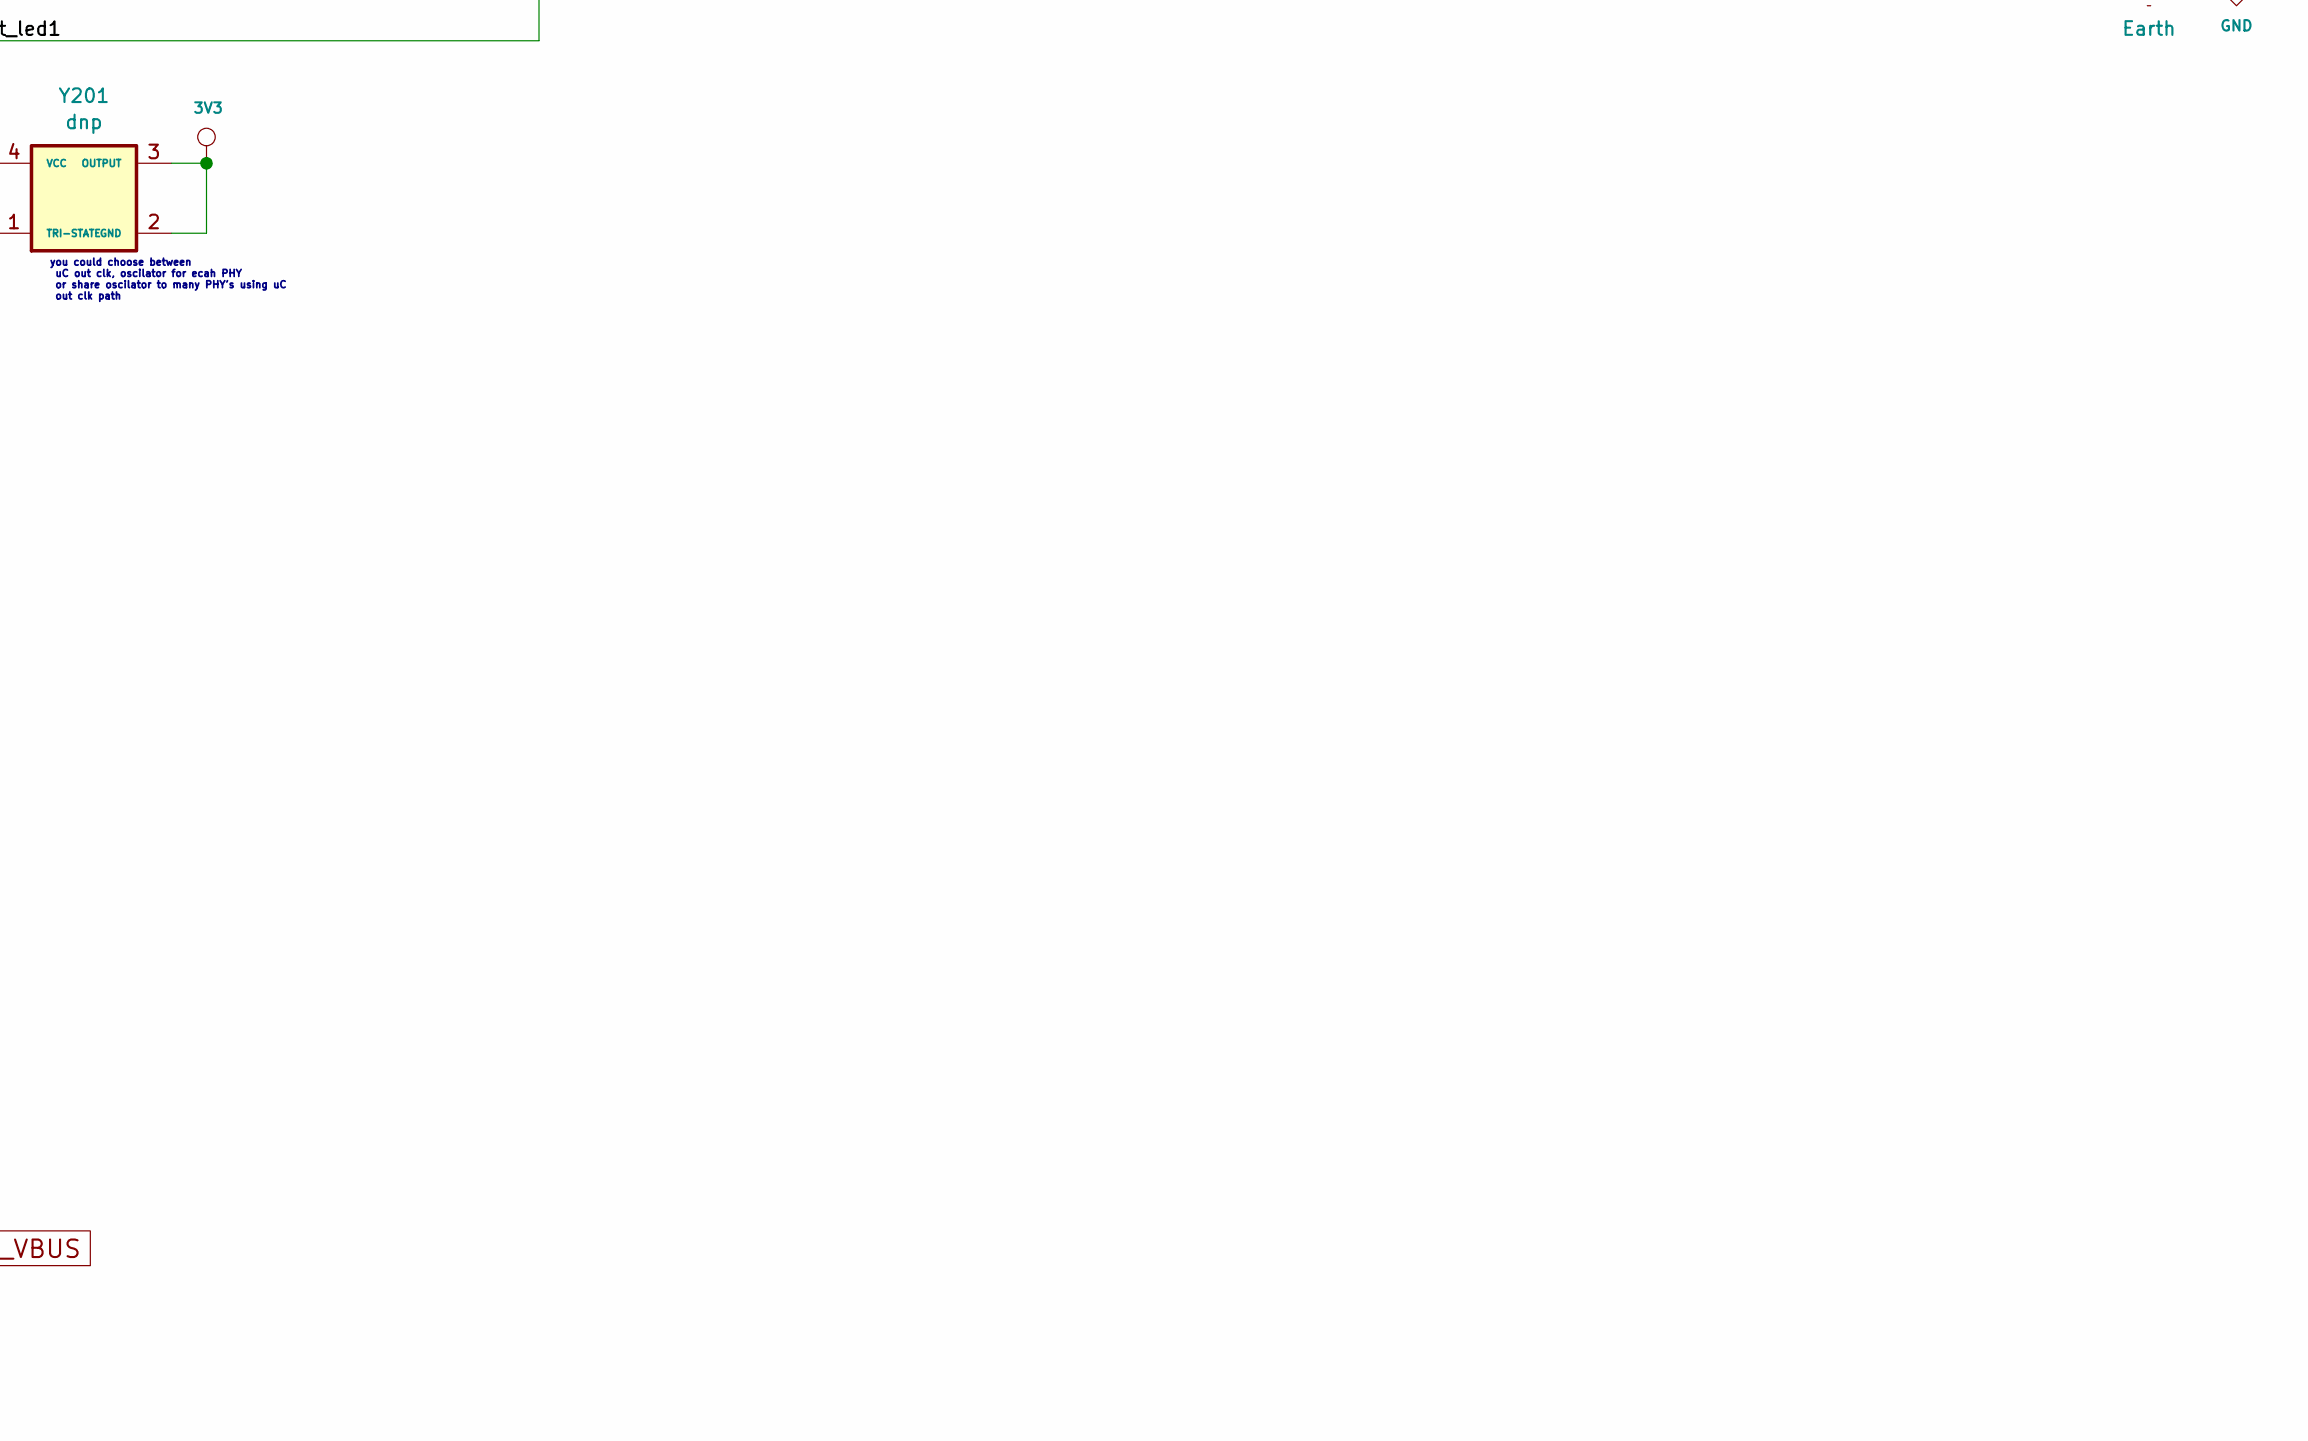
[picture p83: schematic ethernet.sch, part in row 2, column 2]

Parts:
C201, C208: 0.01uF; C_0603_1608Metric
C202, C207, C209, C211, C214, C216: 0.1uF; C_0603_1608Metric
C203, C206, C210, C212, C213, C215: 1uF; C_0603_1608Metric
C204, C205: 10uF; C_0603_1608Metric
C217: 4n7; C_1206_3216Metric
IC201: TPD4E001QDBV; SOT-23-6
J201: 0821-1X1T-36-F; BEL_0821-1X1T-36-F
R201: 4.87k; R_0603_1608Metric
R202: 10.0k; R_0603_1608Metric
R203: 0e; R_0603_1608Metric
R204, R208, R211: 2.2k; R_0603_1608Metric
R205, R206, R207, R209: 49.9; R_0603_1608Metric
R210: 1oe; R_1206_3216Metric_Pad1.42x1.75mm_HandSolder
R212, R213: 470; R_0603_1608Metric
U201: DP83822; QFN-32-1EP_5x5mm_P0.5mm_EP2.9x2.9mm_ThermalVias; PartNumber DP83822IRHBR
Y201: dnp; Oscillator_SMD_SeikoEpson_SG210-4Pin_2.5x2.0mm

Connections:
3V3: C201.2 (Capacitor), C202.2 (Capacitor), C203.1, C204.1, C205.1, C206.1, C207.1, C208.1, C209.1, C210.1, C211.1, C212.1, C213.2 (Capacitor), C214.2 (Capacitor), C215.2 (Capacitor), C216.2 (Capacitor), J201.7 (TCT), J201.12 (RCT), R202.2, R204.2, R205.1, R206.1, R207.1, R208.1, R209.1, R211.1, R212.1, R213.1, U201.14 (AVD33), U201.21 (VDDIO), Y201.2 (GND), Y201.3 (OUTPUT); also elsewhere on the board
5VC: IC201.5 (VCC), R210.1; also elsewhere on the board
/ethernet/P0_RD_N: J201.11 (RD-), R209.2, U201.9 (RD_M)
/ethernet/P0_RD_P: J201.10 (RD+), R207.2, U201.10 (RD_P)
/ethernet/P0_TD_N: J201.9 (TD-), R206.2, U201.11 (TD_M)
/ethernet/P0_TD_P: J201.8 (TD+), R205.2, U201.12 (TD_P)
/ethernet/clk_xi: R203.1, U201.23 (XI), Y201.4 (VCC)
/ethernet/enet_led0: J201.13 (YC), R208.2, U201.17 (LED_0/AN_0/MLED)
/ethernet/enet_led1: J201.16 (GA_OC), R211.2, U201.24 (LED_1)
/ethernet/nc13: U201.13 (NC)
/ethernet/nc15: U201.15 (NC)
/ethernet/nc22: U201.22 (XO)
ENET_CAT_XI: R203.2; also elsewhere on the board
ENET_COL: U201.29 (COL/PHYAD0/MLED); also elsewhere on the board
ENET_CRS: U201.27 (CRS/CRS_DV/LED_CFG); also elsewhere on the board
ENET_MDCLK: U201.20 (MDC); also elsewhere on the board
ENET_MDIO: R204.1, U201.19 (MDIO); also elsewhere on the board
ENET_PWDN: R202.1, U201.8 (INT/~PWDN); also elsewhere on the board
ENET_RST: U201.18 (RESET); also elsewhere on the board
ENET_RX_CLK: U201.25 (RX_CLK); also elsewhere on the board
ENET_RX_D0: U201.30 (RX_D0/PHYAD1); also elsewhere on the board
ENET_RX_D1: U201.31 (RX_D1/PHYAD2); also elsewhere on the board
ENET_RX_D2: U201.32 (RX_D2/PHYAD3); also elsewhere on the board
ENET_RX_D3: U201.1 (RX_D3/PHYAD4/CLKOUT); also elsewhere on the board
ENET_RX_DV: U201.26 (RX_DV/MII_MODE); also elsewhere on the board
ENET_RX_ER: U201.28 (RX_ER/AMDIX_EN); also elsewhere on the board
ENET_TX_CLK: U201.2 (TX_CLK); also elsewhere on the board
ENET_TX_D0: U201.4 (TX_D0); also elsewhere on the board
ENET_TX_D1: U201.5 (TX_D1); also elsewhere on the board
ENET_TX_D2: U201.6 (TX_D2); also elsewhere on the board
ENET_TX_D3: U201.7 (TX_D3); also elsewhere on the board
ENET_TX_EN: U201.3 (TX_EN); also elsewhere on the board
Earth: C217.2 (Capacitor), J201.5 (SHIELD), J201.6 (SHIELD), J201.17 (SHIELD), J201.18 (SHIELD), J201.19 (SHIELD), J201.20 (SHIELD); also elsewhere on the board
GND: C201.1, C202.1, C203.2 (Capacitor), C204.2 (Capacitor), C205.2 (Capacitor), C206.2 (Capacitor), C207.2 (Capacitor), C208.2 (Capacitor), C209.2 (Capacitor), C210.2 (Capacitor), C211.2 (Capacitor), C212.2 (Capacitor), C213.1, C214.1, C215.1, C216.1, C217.1, IC201.2 (GND), J201.4 (GND), R201.2, U201.33 (PAD), Y201.1 (TRI-STATE); also elsewhere on the board
unnamed: J201.14 (YA), R212.2
unnamed: J201.15 (GC_OA), R213.2
unnamed: R201.1, U201.16 (RBIAS)
USB_D+: IC201.3 (IO2), J201.3 (D+); also elsewhere on the board
USB_D-: IC201.1 (IO1), J201.2 (D-); also elsewhere on the board
USB_VBUS: J201.1 (VBUS), R210.2

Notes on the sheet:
EtherNET
you could choose between uC out clk, oscilator for ecah PHY or share oscilator to many PHY's using uC out clk path
the pullup of led_0 is mandatory, but to drive the led you could choose between PHY or uC populating/unpopulating the resistor
I choose transfeormer spare part instead of the embedded shielded RJ45 plus leds, cause noy I can choose any format connector RJ45 and maybe add PoE then. And are halt the price
USB HOST
it's just an USB protection
have interna l 60k pullip

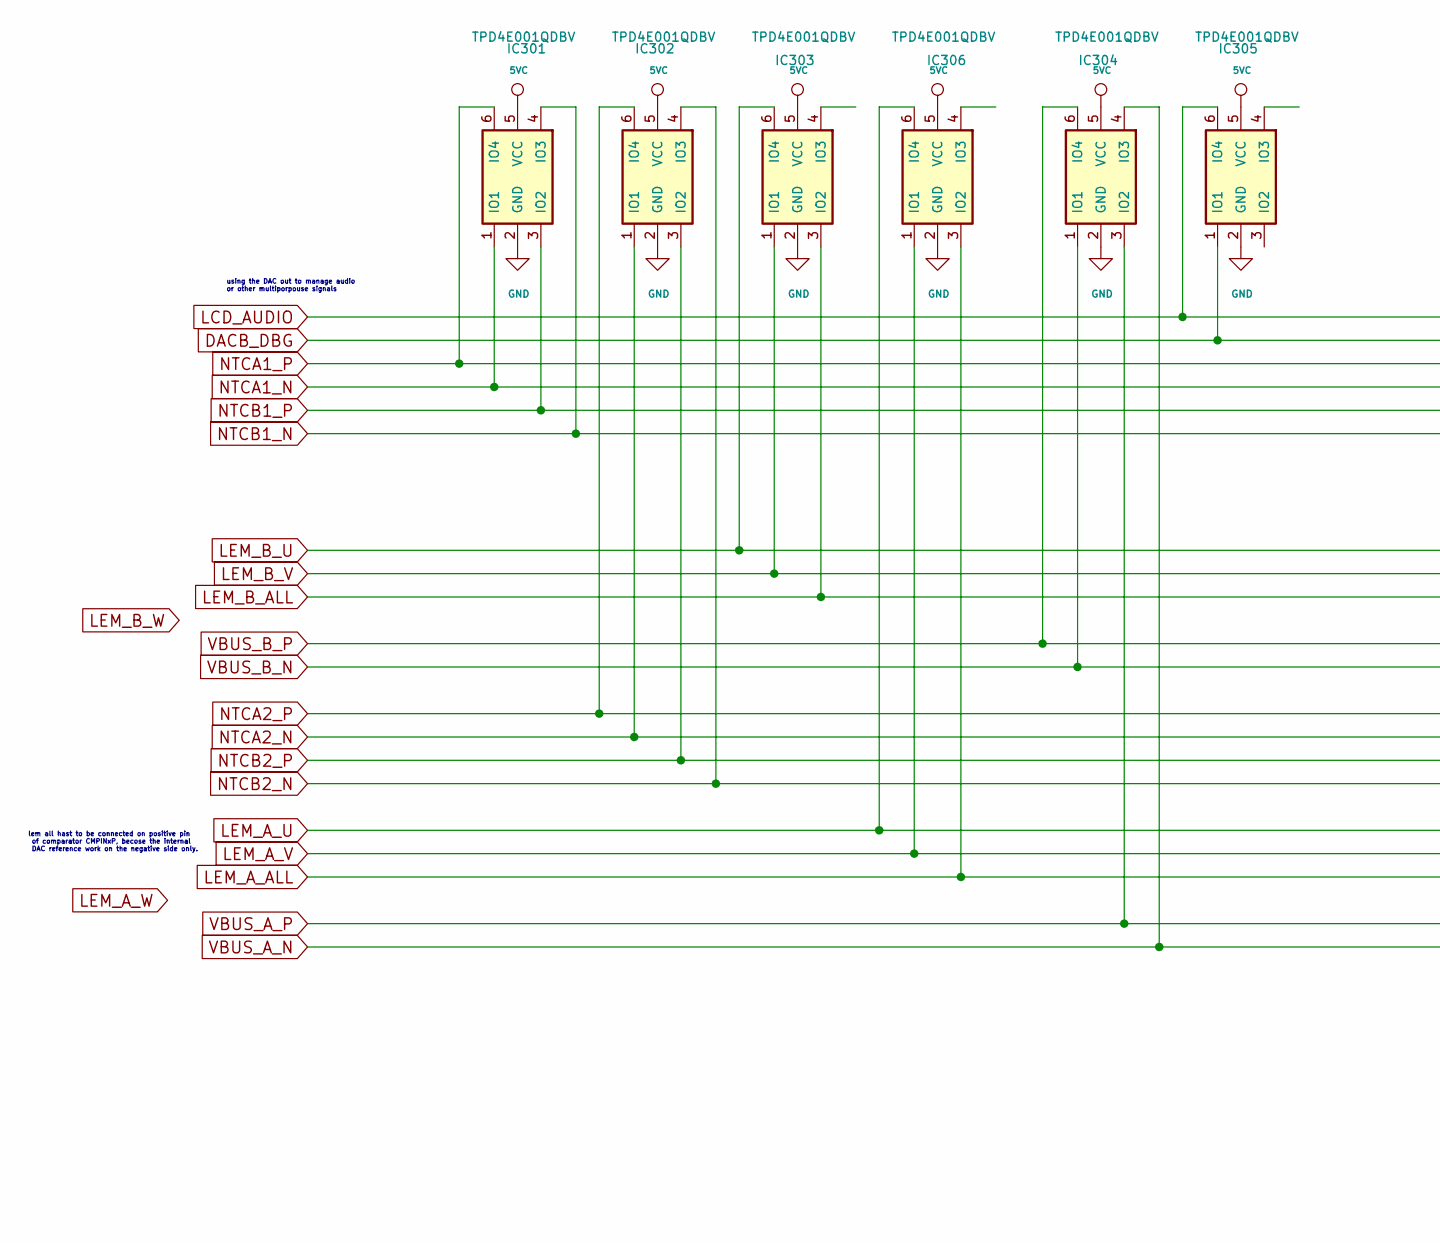
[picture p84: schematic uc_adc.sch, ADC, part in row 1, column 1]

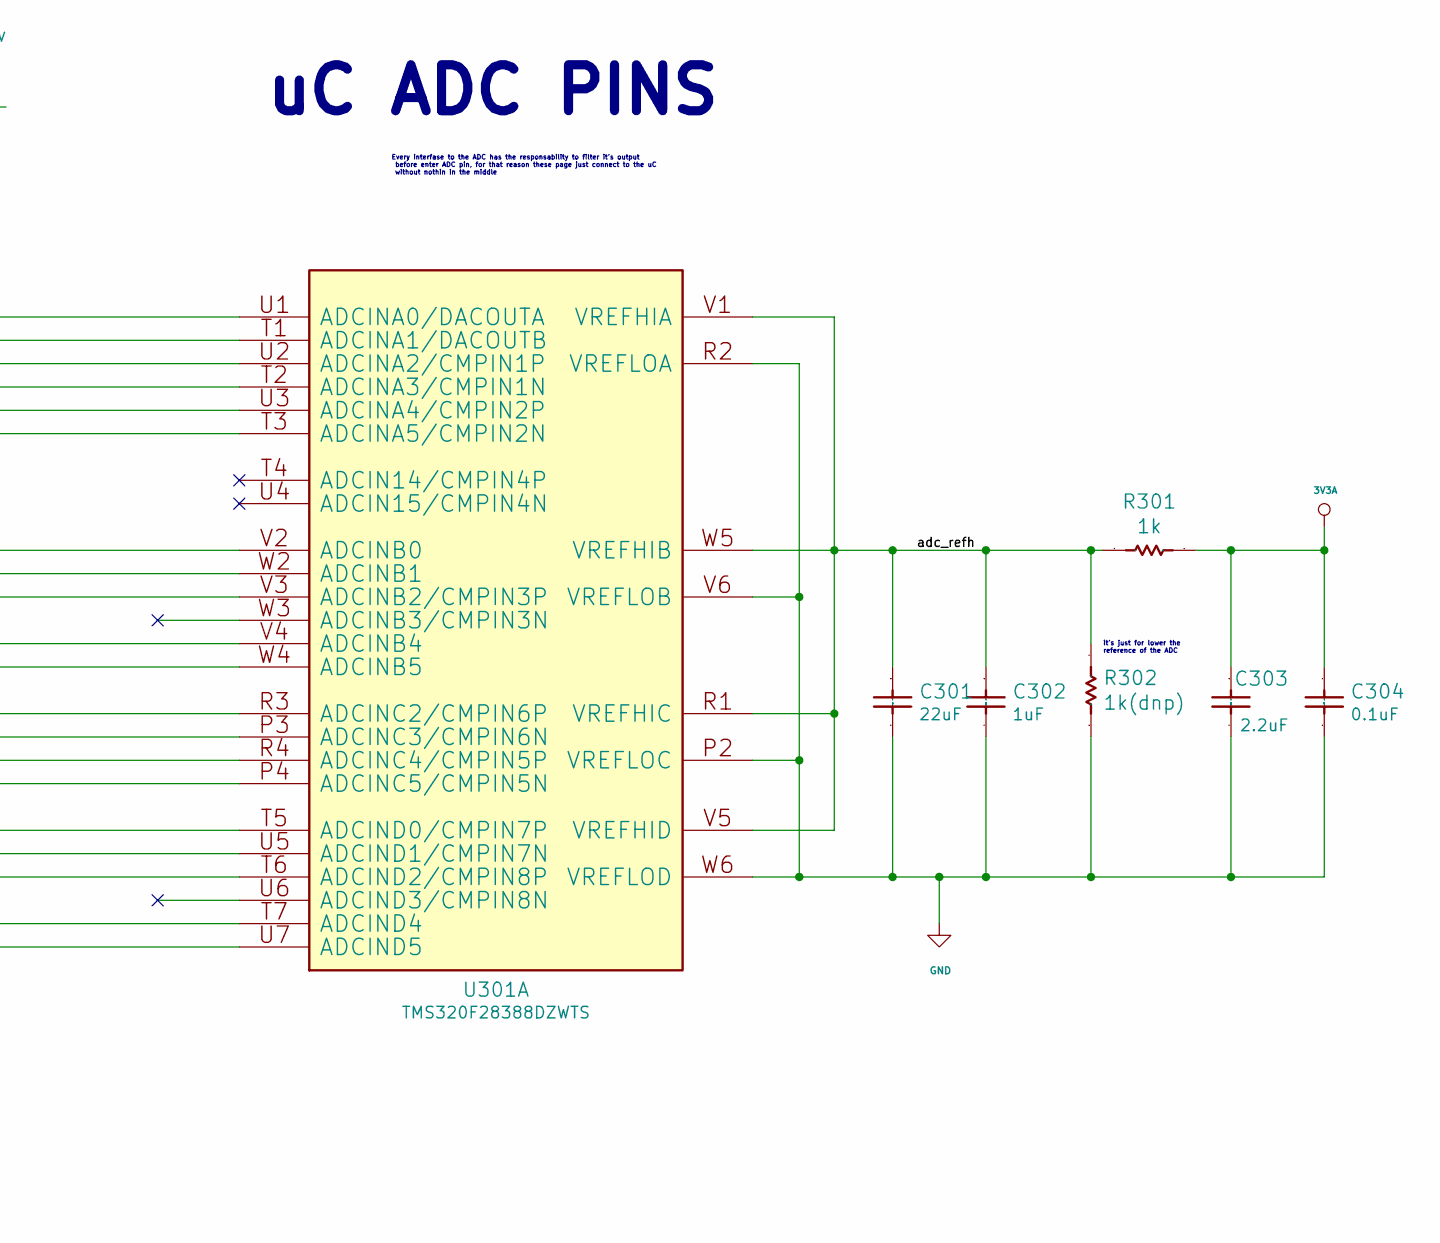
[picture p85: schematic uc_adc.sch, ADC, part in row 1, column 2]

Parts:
C301: 22uF; C_0603_1608Metric
C302: 1uF; C_0603_1608Metric
C303: 2.2uF; C_0603_1608Metric
C304: 0.1uF; C_0603_1608Metric
IC301, IC302, IC303, IC304, IC305, IC306: TPD4E001QDBV; SOT-23-6
R301: 1k; R_0603_1608Metric
R302: 1k(dnp); R_0603_1608Metric
U301: TMS320F28388DZWTS; BGA337CP80_19X19_1600X1600X140B50N; PartNumber TMS320F28388DZWTS

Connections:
3V3A: C303.1, C304.1, R301.1; also elsewhere on the board
5VC: IC301.5 (VCC), IC302.5 (VCC), IC303.5 (VCC), IC304.5 (VCC), IC305.5 (VCC), IC306.5 (VCC); also elsewhere on the board
/uc_adc/adc_refh: C301.1, C302.1, R301.2, R302.2, U301.R1 (VREFHIC), U301.V1 (VREFHIA), U301.V5 (VREFHID), U301.W5 (VREFHIB)
DACB_DBG: IC305.1 (IO1), U301.T1 (ADCINA1/DACOUTB); also elsewhere on the board
GND: C301.2 (Capacitor), C302.2 (Capacitor), C303.2 (Capacitor), C304.2 (Capacitor), IC301.2 (GND), IC302.2 (GND), IC303.2 (GND), IC304.2 (GND), IC305.2 (GND), IC306.2 (GND), R302.1, U301.P2 (VREFLOC), U301.R2 (VREFLOA), U301.V6 (VREFLOB), U301.W6 (VREFLOD); also elsewhere on the board
LCD_AUDIO: IC305.6 (IO4), U301.U1 (ADCINA0/DACOUTA); also elsewhere on the board
LEM_A_ALL: IC306.3 (IO2), U301.T6 (ADCIND2/CMPIN8P); also elsewhere on the board
LEM_A_U: IC306.6 (IO4), U301.T5 (ADCIND0/CMPIN7P); also elsewhere on the board
LEM_A_V: IC306.1 (IO1), U301.U5 (ADCIND1/CMPIN7N); also elsewhere on the board
LEM_B_ALL: IC303.3 (IO2), U301.V3 (ADCINB2/CMPIN3P); also elsewhere on the board
LEM_B_U: IC303.6 (IO4), U301.V2 (ADCINB0); also elsewhere on the board
LEM_B_V: IC303.1 (IO1), U301.W2 (ADCINB1); also elsewhere on the board
NTCA1_N: IC301.1 (IO1), U301.T2 (ADCINA3/CMPIN1N); also elsewhere on the board
NTCA1_P: IC301.6 (IO4), U301.U2 (ADCINA2/CMPIN1P); also elsewhere on the board
NTCA2_N: IC302.1 (IO1), U301.P3 (ADCINC3/CMPIN6N); also elsewhere on the board
NTCA2_P: IC302.6 (IO4), U301.R3 (ADCINC2/CMPIN6P); also elsewhere on the board
NTCB1_N: IC301.4 (IO3), U301.T3 (ADCINA5/CMPIN2N); also elsewhere on the board
NTCB1_P: IC301.3 (IO2), U301.U3 (ADCINA4/CMPIN2P); also elsewhere on the board
NTCB2_N: IC302.4 (IO3), U301.P4 (ADCINC5/CMPIN5N); also elsewhere on the board
NTCB2_P: IC302.3 (IO2), U301.R4 (ADCINC4/CMPIN5P); also elsewhere on the board
VBUS_A_N: IC304.4 (IO3), U301.U7 (ADCIND5); also elsewhere on the board
VBUS_A_P: IC304.3 (IO2), U301.T7 (ADCIND4); also elsewhere on the board
VBUS_B_N: IC304.1 (IO1), U301.W4 (ADCINB5); also elsewhere on the board
VBUS_B_P: IC304.6 (IO4), U301.V4 (ADCINB4); also elsewhere on the board

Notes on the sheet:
lem all hast to be connected on positive pin of comparator CMPINxP, becose the internal DAC reference work on the negative side only.
uC ADC PINS
Every interfase to the ADC has the responsability to filter it's output before enter ADC pin, for that reason these page just connect to the uC without nothin in the middle
using the DAC out to manage audio or other multiporpouse signals
it's just for lower the reference of the ADC

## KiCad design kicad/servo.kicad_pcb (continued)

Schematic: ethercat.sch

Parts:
C401, C402, C416, C417: 0.01uF; C_0603_1608Metric
C403, C404, C413, C414, C415, C418, C419, C422, C423: 0.1uF; C_0603_1608Metric
C405, C406, C411, C412, C420, C421, C424, C425, C426, C427, C428, C429, C430, C431, C432, C433: 1uF; C_0603_1608Metric
C407, C408, C409, C410: 10uF; C_0603_1608Metric
C434: 4n7; C_1206_3216Metric
D401: Red@2mA; LED_0603_1608Metric
D402: green@2mA; LED_0603_1608Metric
R401, R402, R403, R404, R405, R406, R407, R408, R409, R410, R411, R412, R413, R414, R415, R416, R427, R433, R434: 2.2k; R_0603_1608Metric
R417, R418: 4.7k; R_0603_1608Metric
R419, R420: 330; R_0603_1608Metric
R421, R424: 4.87k; R_0603_1608Metric
R422, R425: 10.0k; R_0603_1608Metric
R423, R426: 0e; R_0603_1608Metric
R429, R430, R431, R432, R435, R437, R438, R440: 49.9; R_0603_1608Metric
R436, R439: 0e(dnp); R_0603_1608Metric
R441, R442, R445, R446: 470; R_0603_1608Metric
U401: CAT24C16WI; SOIC-8_3.9x4.9mm_P1.27mm
U402, U403: DP83822; QFN-32-1EP_5x5mm_P0.5mm_EP2.9x2.9mm_ThermalVias; PartNumber DP83822IRHBR
U404: rj45x2; rj45x2_0845-2G1T-H5
Y401, Y402: dnp; Oscillator_SMD_SeikoEpson_SG210-4Pin_2.5x2.0mm

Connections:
3V3: C401.2 (Capacitor), C402.2 (Capacitor), C403.2 (Capacitor), C404.2 (Capacitor), C405.1, C406.1, C407.1, C408.1, C409.1, C410.1, C411.1, C412.1, C413.1, C414.1, C415.1, C416.1, C417.1, C418.1, C419.1, C420.1, C421.1, C422.1, C423.1, C424.1, C425.1, C426.2 (Capacitor), C427.2 (Capacitor), C428.2 (Capacitor), C429.2 (Capacitor), C430.2 (Capacitor), C431.2 (Capacitor), C432.2 (Capacitor), C433.2 (Capacitor), R412.1, R413.1, R414.1, R415.1, R416.1, R417.1, R418.1, R419.2, R420.2, R422.2, R425.2, R427.1, R429.1, R430.1, R431.1, R432.1, R433.1, R434.1, R435.1, R437.1, R438.1, R440.1, R441.1, R442.1, R445.1, R446.1, U401.8 (VCC), U402.14 (AVD33), U402.21 (VDDIO), U403.14 (AVD33), U403.21 (VDDIO), U404.2 (TCT), U404.5 (TCT), U404.9 (TCT), U404.12 (TCT), Y401.1 (TRI-STATE), Y401.4 (VCC), Y402.2 (GND), Y402.3 (OUTPUT); also elsewhere on the board
/ethercat/P0_RD_N: R437.2, U402.9 (RD_M), U404.13 (RD-)
/ethercat/P0_RD_P: R435.2, U402.10 (RD_P), U404.11 (RD+)
/ethercat/P0_TD_N: R431.2, U402.11 (TD_M), U404.10 (TD-)
/ethercat/P0_TD_P: R429.2, U402.12 (TD_P), U404.8 (TD+)
/ethercat/P1_RD_N: R440.2, U403.9 (RD_M), U404.6 (RD-)
/ethercat/P1_RD_P: R438.2, U403.10 (RD_P), U404.4 (RD+)
/ethercat/P1_TD_N: R432.2, U403.11 (TD_M), U404.3 (TD-)
/ethercat/P1_TD_P: R430.2, U403.12 (TD_P), U404.1 (TD+)
/ethercat/ecat0_col: R410.2, U402.29 (COL/PHYAD0/MLED)
/ethercat/ecat0_crs: R413.2, U402.27 (CRS/CRS_DV/LED_CFG)
/ethercat/ecat1_col: R412.2, U403.29 (COL/PHYAD0/MLED)
/ethercat/ecat1_crs: R414.2, U403.27 (CRS/CRS_DV/LED_CFG)
ECAT0_RJ_LED0: R436.2, U404.20 (Led-); also elsewhere on the board
ECAT0_RJ_LED1: U404.22 (Led-); also elsewhere on the board
ECAT0_RX_CLK: U402.25 (RX_CLK); also elsewhere on the board
ECAT0_RX_D0: R402.2, U402.30 (RX_D0/PHYAD1); also elsewhere on the board
ECAT0_RX_D1: R404.2, U402.31 (RX_D1/PHYAD2); also elsewhere on the board
ECAT0_RX_D2: R406.2, U402.32 (RX_D2/PHYAD3); also elsewhere on the board
ECAT0_RX_D3: R408.2, U402.1 (RX_D3/PHYAD4/CLKOUT); also elsewhere on the board
ECAT0_RX_DV: R401.2, U402.26 (RX_DV/MII_MODE); also elsewhere on the board
ECAT0_RX_ER: R415.2, U402.28 (RX_ER/AMDIX_EN); also elsewhere on the board
ECAT0_TX_CLK: U402.2 (TX_CLK); also elsewhere on the board
ECAT0_TX_D0: U402.4 (TX_D0); also elsewhere on the board
ECAT0_TX_D1: U402.5 (TX_D1); also elsewhere on the board
ECAT0_TX_D2: U402.6 (TX_D2); also elsewhere on the board
ECAT0_TX_D3: U402.7 (TX_D3); also elsewhere on the board
ECAT0_TX_EN: U402.3 (TX_EN); also elsewhere on the board
ECAT1_RJ_LED0: U404.18 (Led-); also elsewhere on the board
ECAT1_RJ_LED1: R439.2, U404.16 (Led-); also elsewhere on the board
ECAT1_RX_CLK: U403.25 (RX_CLK); also elsewhere on the board
ECAT1_RX_D0: R405.2, U403.30 (RX_D0/PHYAD1); also elsewhere on the board
ECAT1_RX_D1: R407.2, U403.31 (RX_D1/PHYAD2); also elsewhere on the board
ECAT1_RX_D2: R409.2, U403.32 (RX_D2/PHYAD3); also elsewhere on the board
ECAT1_RX_D3: R411.2, U403.1 (RX_D3/PHYAD4/CLKOUT); also elsewhere on the board
ECAT1_RX_DV: R403.2, U403.26 (RX_DV/MII_MODE); also elsewhere on the board
ECAT1_RX_ER: R416.2, U403.28 (RX_ER/AMDIX_EN); also elsewhere on the board
ECAT1_TX_CLK: U403.2 (TX_CLK); also elsewhere on the board
ECAT1_TX_D0: U403.4 (TX_D0); also elsewhere on the board
ECAT1_TX_D1: U403.5 (TX_D1); also elsewhere on the board
ECAT1_TX_D2: U403.6 (TX_D2); also elsewhere on the board
ECAT1_TX_D3: U403.7 (TX_D3); also elsewhere on the board
ECAT1_TX_EN: U403.3 (TX_EN); also elsewhere on the board
ECAT_EEPROM_SCL: R418.2, U401.6 (SCL); also elsewhere on the board
ECAT_EEPROM_SDA: R417.2, U401.5 (SDA); also elsewhere on the board
ECAT_LED_ERR: D402.1 (K); also elsewhere on the board
ECAT_LED_RUN: D401.1 (K); also elsewhere on the board
ECAT_MDCLK: U402.20 (MDC), U403.20 (MDC); also elsewhere on the board
ECAT_MDIO: R427.2, U402.19 (MDIO), U403.19 (MDIO); also elsewhere on the board
ECAT_RST: U402.18 (RESET), U403.18 (RESET); also elsewhere on the board
ENET_CAT_XI: R423.2, R426.2; also elsewhere on the board
Earth: C434.2 (Capacitor), U404.7 (Gnd), U404.14 (Gnd); also elsewhere on the board
GND: C401.1, C402.1, C403.1, C404.1, C405.2 (Capacitor), C406.2 (Capacitor), C407.2 (Capacitor), C408.2 (Capacitor), C409.2 (Capacitor), C410.2 (Capacitor), C411.2 (Capacitor), C412.2 (Capacitor), C413.2 (Capacitor), C414.2 (Capacitor), C415.2 (Capacitor), C416.2 (Capacitor), C417.2 (Capacitor), C418.2 (Capacitor), C419.2 (Capacitor), C420.2 (Capacitor), C421.2 (Capacitor), C422.2 (Capacitor), C423.2 (Capacitor), C424.2 (Capacitor), C425.2 (Capacitor), C426.1, C427.1, C428.1, C429.1, C430.1, C431.1, C432.1, C433.1, C434.1, R401.1, R402.1, R403.1, R404.1, R405.1, R406.1, R407.1, R408.1, R409.1, R410.1, R411.1, R421.2, R424.2, U401.1 (NC), U401.2 (NC), U401.3 (NC), U401.4 (VSS), U401.7 (WP), U402.33 (PAD), U403.33 (PAD), Y401.2 (GND), Y402.1 (TRI-STATE); also elsewhere on the board
unnamed: D401.2 (A), R419.1
unnamed: D402.2 (A), R420.1
unnamed: R421.1, U402.16 (RBIAS)
unnamed: R422.1, U402.8 (INT/~PWDN)
unnamed: R423.1, U402.23 (XI), Y401.3 (OUTPUT)
unnamed: R424.1, U403.16 (RBIAS)
unnamed: R425.1, U403.8 (INT/~PWDN)
unnamed: R426.1, U403.23 (XI), Y402.4 (VCC)
unnamed: R433.2, R436.1, U402.17 (LED_0/AN_0/MLED)
unnamed: R434.2, R439.1, U403.17 (LED_0/AN_0/MLED)
unnamed: R441.2, U404.17 (Led+)
unnamed: R442.2, U404.15 (Led+)
unnamed: R445.2, U404.21 (Led+)
unnamed: R446.2, U404.19 (Led+)

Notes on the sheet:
EtherCAT P1
EtherCAT EEPROM
Run and Error LEDs
EtherCAT P0
Address select. Be shure you select two distinct
these IC is a 'must'. Especified on the ethercat slave
EtherCAT
you could choose between uC out clk, oscilator for ecah PHY or share oscilator to many PHY's using uC out clk path
the pullup of led_0 is mandatory, but to drive the led you could choose between PHY or uC populating/unpopulating the resistor
It'd be optionall
I choose transfeormer spare part instead of the embedded shielded RJ45 plus leds, cause noy I can choose any format connector RJ45 and maybe add PoE then. And are halt the price The eeprom is mandatory in order to ESC read save some internal configuration. Leds are optional, but the PHY's has som p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
2k2 pullup as indicated by phy IC's
25Mhz!!
It's a good idea to have them on these fitst stage but could be throught away on next release.

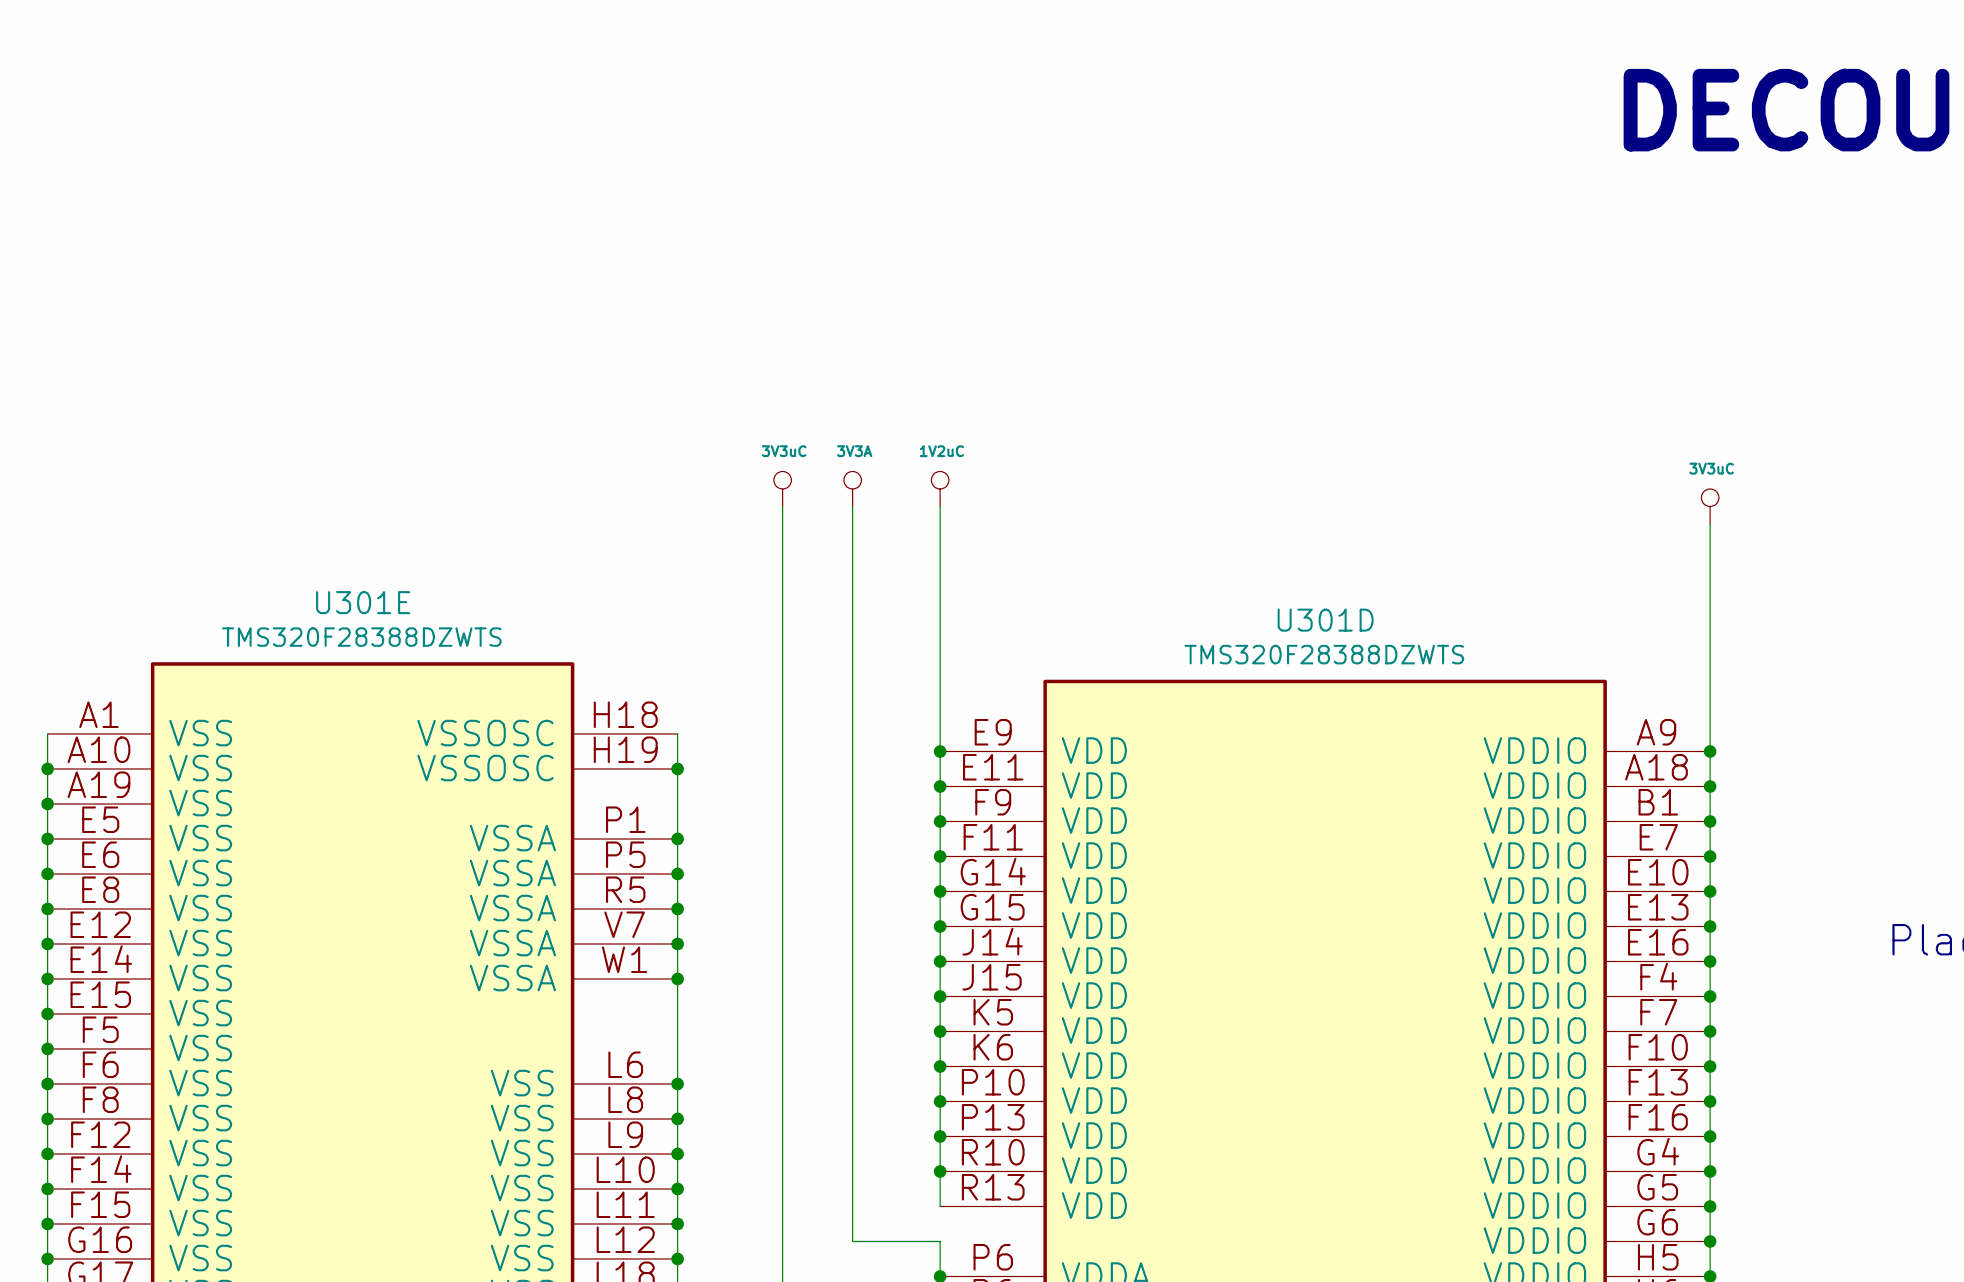
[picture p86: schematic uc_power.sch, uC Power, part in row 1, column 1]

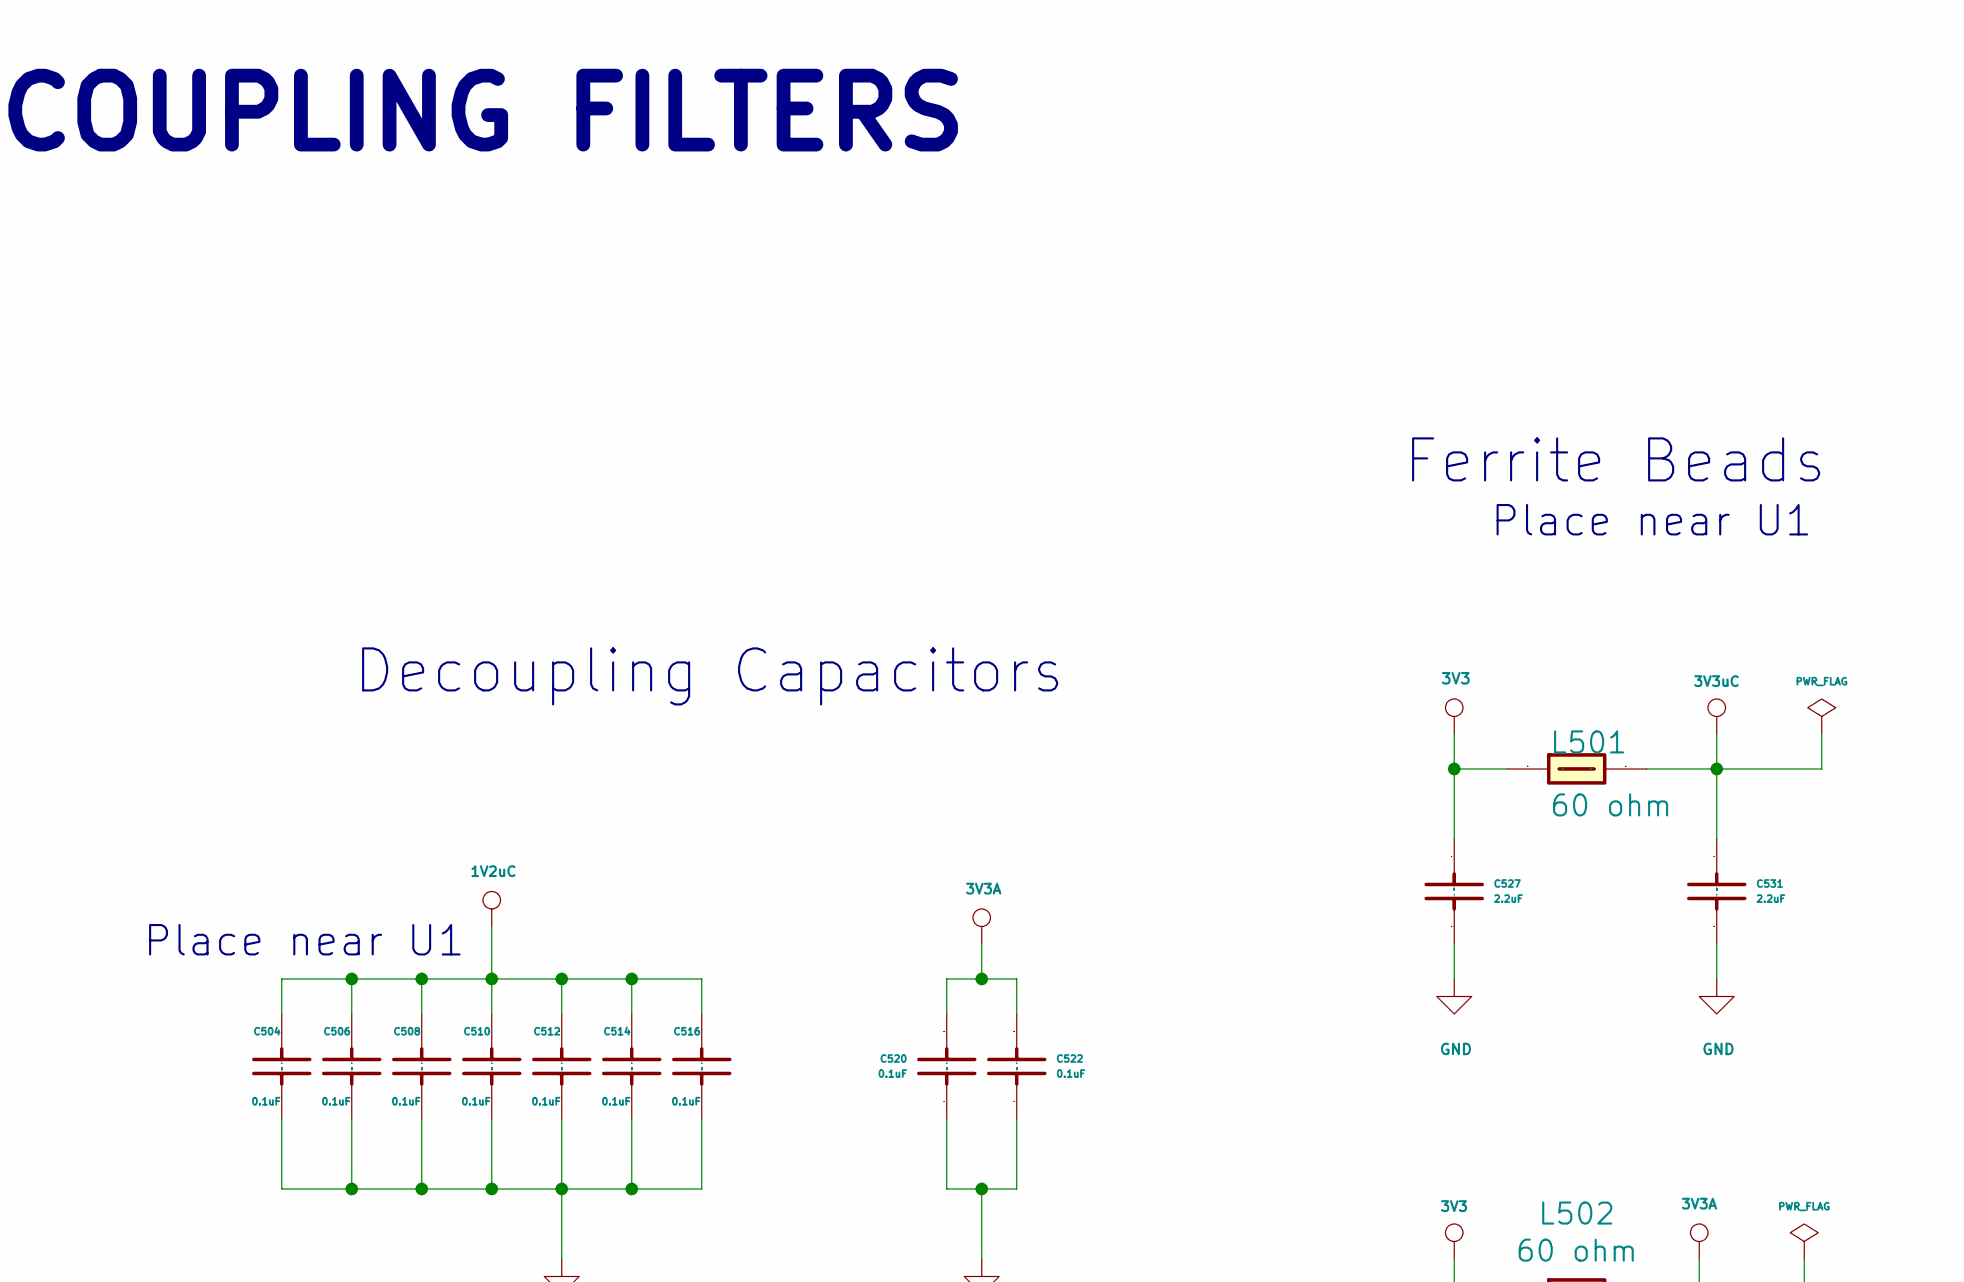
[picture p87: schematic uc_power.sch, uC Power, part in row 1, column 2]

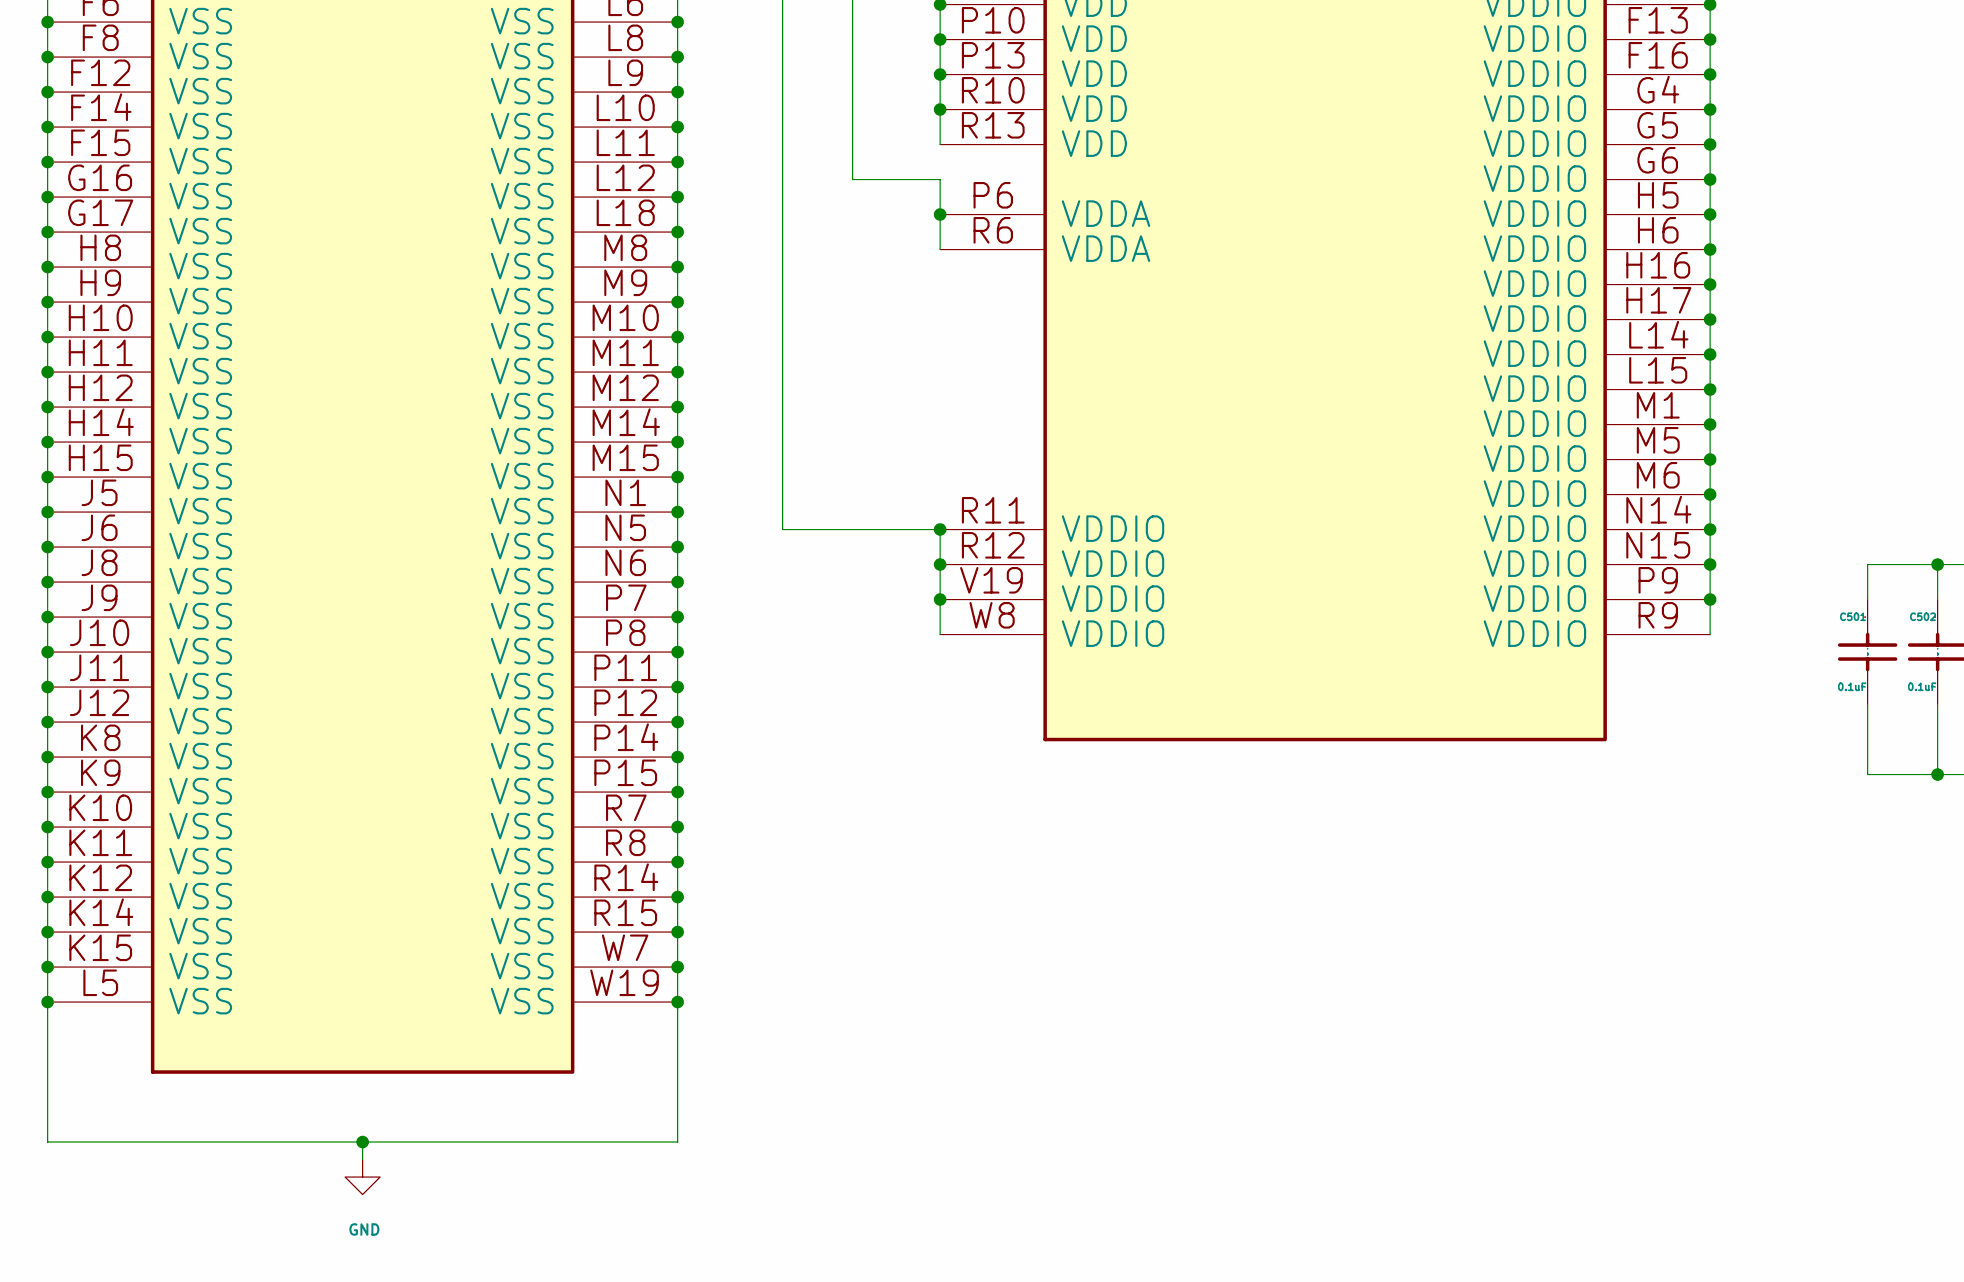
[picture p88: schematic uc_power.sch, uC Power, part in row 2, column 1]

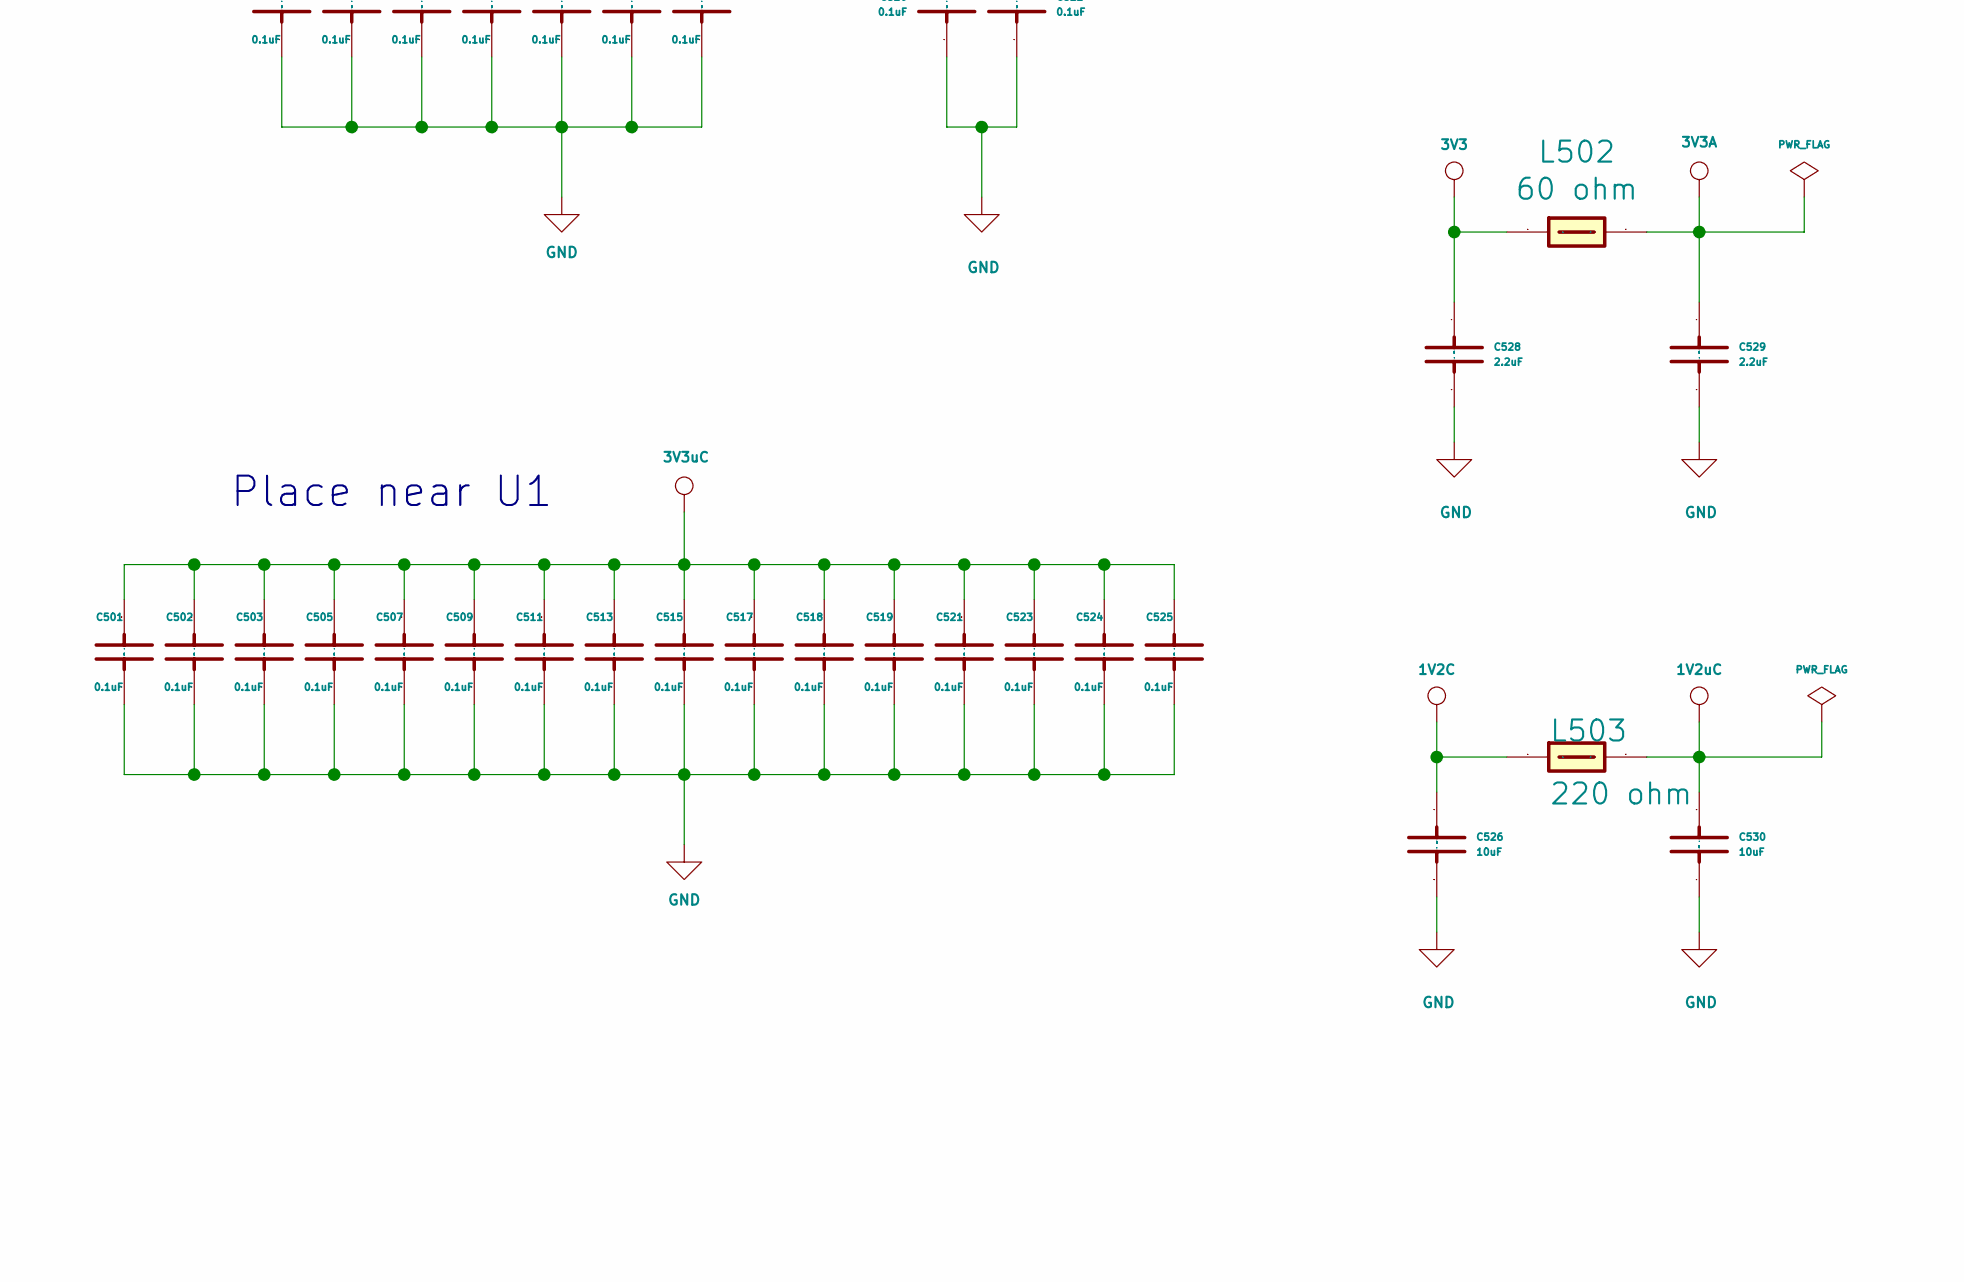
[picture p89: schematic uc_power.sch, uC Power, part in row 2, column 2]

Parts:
C501, C502, C503, C504, C505, C506, C507, C508, C509, C510, C511, C512, C513, C514, C515, C516, C517, C518, C519, C520, C521, C522, C523, C524, C525: 0.1uF; C_0603_1608Metric
C526, C530: 10uF; C_0603_1608Metric
C527, C528, C529, C531: 2.2uF; C_0603_1608Metric
L501, L502: 60 ohm; L_1206_3216Metric_Pad1.42x1.75mm_HandSolder
L503: 220 ohm; L_1206_3216Metric_Pad1.42x1.75mm_HandSolder
U301: TMS320F28388DZWTS; BGA337CP80_19X19_1600X1600X140B50N; PartNumber TMS320F28388DZWTS

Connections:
1V2: C504.1, C506.1, C508.1, C510.1, C512.1, C514.1, C516.1, C530.1, L503.2, U301.E9 (VDD), U301.E11 (VDD), U301.F9 (VDD), U301.F11 (VDD), U301.G14 (VDD), U301.G15 (VDD), U301.J14 (VDD), U301.J15 (VDD), U301.K5 (VDD), U301.K6 (VDD), U301.P10 (VDD), U301.P13 (VDD), U301.R10 (VDD), U301.R13 (VDD)
1V2C: C526.2 (Capacitor), L503.1; also elsewhere on the board
3V3: C527.2 (Capacitor), C528.2 (Capacitor), L501.1, L502.1; also elsewhere on the board
3V3A: C520.1, C522.1, C529.2 (Capacitor), L502.2, U301.P6 (VDDA), U301.R6 (VDDA); also elsewhere on the board
GND: C501.2 (Capacitor), C502.2 (Capacitor), C503.2 (Capacitor), C504.2 (Capacitor), C505.2 (Capacitor), C506.2 (Capacitor), C507.2 (Capacitor), C508.2 (Capacitor), C509.2 (Capacitor), C510.2 (Capacitor), C511.2 (Capacitor), C512.2 (Capacitor), C513.2 (Capacitor), C514.2 (Capacitor), C515.2 (Capacitor), C516.2 (Capacitor), C517.2 (Capacitor), C518.2 (Capacitor), C519.2 (Capacitor), C520.2 (Capacitor), C521.2 (Capacitor), C522.2 (Capacitor), C523.2 (Capacitor), C524.2 (Capacitor), C525.2 (Capacitor), C526.1, C527.1, C528.1, C529.1, C530.2 (Capacitor), C531.1, U301.A1 (VSS), U301.A10 (VSS), U301.A19 (VSS), U301.E5 (VSS), U301.E6 (VSS), U301.E8 (VSS), U301.E12 (VSS), U301.E14 (VSS), U301.E15 (VSS), U301.F5 (VSS), U301.F6 (VSS), U301.F8 (VSS), U301.F12 (VSS), U301.F14 (VSS), U301.F15 (VSS), U301.G16 (VSS), U301.G17 (VSS), U301.H8 (VSS), U301.H9 (VSS), U301.H10 (VSS), U301.H11 (VSS), U301.H12 (VSS), U301.H14 (VSS), U301.H15 (VSS), U301.H18 (VSSOSC), U301.H19 (VSSOSC), U301.J5 (VSS), U301.J6 (VSS), U301.J8 (VSS), U301.J9 (VSS), U301.J10 (VSS), U301.J11 (VSS), U301.J12 (VSS), U301.K8 (VSS), U301.K9 (VSS), U301.K10 (VSS), U301.K11 (VSS), U301.K12 (VSS), U301.K14 (VSS), U301.K15 (VSS), U301.L5 (VSS), U301.L6 (VSS), U301.L8 (VSS), U301.L9 (VSS), U301.L10 (VSS), U301.L11 (VSS), U301.L12 (VSS), U301.L18 (VSS), U301.M8 (VSS), U301.M9 (VSS), U301.M10 (VSS), U301.M11 (VSS), U301.M12 (VSS), U301.M14 (VSS), U301.M15 (VSS), U301.N1 (VSS), U301.N5 (VSS), U301.N6 (VSS), U301.P1 (VSSA), U301.P5 (VSSA), U301.P7 (VSS), U301.P8 (VSS), U301.P11 (VSS), U301.P12 (VSS), U301.P14 (VSS), U301.P15 (VSS), U301.R5 (VSSA), U301.R7 (VSS), U301.R8 (VSS), U301.R14 (VSS), U301.R15 (VSS), U301.V7 (VSSA), U301.W1 (VSSA), U301.W7 (VSS), U301.W19 (VSS); also elsewhere on the board
IN_3V3C: C501.1, C502.1, C503.1, C505.1, C507.1, C509.1, C511.1, C513.1, C515.1, C517.1, C518.1, C519.1, C521.1, C523.1, C524.1, C525.1, C531.2 (Capacitor), L501.2, U301.A9 (VDDIO), U301.A18 (VDDIO), U301.B1 (VDDIO), U301.E7 (VDDIO), U301.E10 (VDDIO), U301.E13 (VDDIO), U301.E16 (VDDIO), U301.F4 (VDDIO), U301.F7 (VDDIO), U301.F10 (VDDIO), U301.F13 (VDDIO), U301.F16 (VDDIO), U301.G4 (VDDIO), U301.G5 (VDDIO), U301.G6 (VDDIO), U301.H5 (VDDIO), U301.H6 (VDDIO), U301.H16 (VDDIO), U301.H17 (VDDIO), U301.L14 (VDDIO), U301.L15 (VDDIO), U301.M1 (VDDIO), U301.M5 (VDDIO), U301.M6 (VDDIO), U301.N14 (VDDIO), U301.N15 (VDDIO), U301.P9 (VDDIO), U301.R9 (VDDIO), U301.R11 (VDDIO), U301.R12 (VDDIO), U301.V19 (VDDIO), U301.W8 (VDDIO)

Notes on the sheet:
Place near U1
Decoupling Capacitors
Ferrite Beads
DECOUPLING FILTERS

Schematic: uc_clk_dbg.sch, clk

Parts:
C601: 1nF; C_0603_1608Metric
C602: 0.01uF; C_0603_1608Metric
C603: 0.1uF; C_0603_1608Metric
D603: green; LED_0603_1608Metric
D604: blue; LED_0603_1608Metric
J601: dbg_conn; PinSocket_2x06_P2.54mm_Vertical
R603, R606: 1.0k; R_0603_1608Metric
R604, R605: 56k; R_0805_2012Metric_Pad1.15x1.40mm_HandSolder
R607, R610: 2.2k; R_0603_1608Metric
R608, R609: 680; R_0603_1608Metric
U301: TMS320F28388DZWTS; BGA337CP80_19X19_1600X1600X140B50N; PartNumber TMS320F28388DZWTS
U601: SN74ALVC244PW; TSSOP-20_4.4x6.5mm_P0.65mm
U602: M25PX32-VMW; SOIJ-8_5.3x5.3mm_P1.27mm
Y601: Oscillator_SMD_SeikoEpson_SG210-4Pin_2.5x2.0mm

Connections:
3V3: C603.2 (Capacitor), D603.2 (A), D604.2 (A), J601.2, R604.1, R605.1, R610.2, U601.1 (1~OE), U601.19 (2~OE), U601.20 (VCC), U602.3 (W#/VPP), U602.7 (HOLD#), U602.8 (VCC), Y601.1 (TRI-STATE), Y601.4 (VCC); also elsewhere on the board
5VC: J601.1; also elsewhere on the board
/uc_clk_dbg/F2838x_CLK: U301.G19 (X1), Y601.3 (OUTPUT)
/uc_clk_dbg/MCU_TCK: U301.V15 (TCK), U601.18 (1Y1)
/uc_clk_dbg/MCU_TDI: U301.W13 (TDI), U601.16 (1Y2)
/uc_clk_dbg/MCU_TDO: U301.W15 (TDO), U601.11 (2A1)
/uc_clk_dbg/MCU_TMS: U301.W14 (TMS), U601.14 (1Y3)
/uc_clk_dbg/MCU_TRSTn: R607.2, U301.V14 (TRST), U601.12 (1Y4)
/uc_clk_dbg/MCU_XRSn: C602.1, R610.1, U301.F19 (XRS)
/uc_clk_dbg/PRG_SCI_RX: J601.4, R603.2, U601.5 (2Y3)
/uc_clk_dbg/PRG_SCI_TX: J601.3, U601.17 (2A4)
/uc_clk_dbg/PRG_TCK: J601.12, U601.2 (1A1)
/uc_clk_dbg/PRG_TDI: J601.11, U601.4 (1A2)
/uc_clk_dbg/PRG_TDO: J601.8, U601.9 (2Y1)
/uc_clk_dbg/PRG_TMS: J601.10, U601.6 (1A3)
/uc_clk_dbg/PRG_TRSTn: J601.9, U601.8 (1A4)
BOOT1: R604.2; also elsewhere on the board
BOOT2: R605.2; also elsewhere on the board
DACB_DBG: R608.1; also elsewhere on the board
DACB_DBG_OUT: J601.7, R609.2
FLASH_SPI_CLK: U602.6 (C); also elsewhere on the board
FLASH_SPI_CS: U602.1 (S#); also elsewhere on the board
FLASH_SPI_MISO: U602.2 (DQ1); also elsewhere on the board
FLASH_SPI_MOSI: U602.5 (DQ0); also elsewhere on the board
GND: C601.1, C602.2 (Capacitor), C603.1, J601.5, J601.6, R607.1, U601.10 (GND), U601.13 (2A2), U602.4 (VSS), Y601.2 (GND); also elsewhere on the board
unnamed: C601.2 (Capacitor), R608.2, R609.1
unnamed: D603.1 (K), R603.1
unnamed: D604.1 (K), R606.1
SCIA_RX: R606.2, U601.3 (2Y4); also elsewhere on the board
SCIA_TX: U601.15 (2A3); also elsewhere on the board

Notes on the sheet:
I left fixed in flash mode if you need to change it you'll get dirty
25MHz Clock
Reset
SPI FLASH
To store some firmware features, and maybe UI images or screens
ADC/DAC DBG OUT
it's just optional for debug porpouses to monitor some analog signal out from the board, it could be very handy
Programmer connector plus SCI for debug porpouses.. take in account that it's not isolated, only buffered to minimize risk. It's supoussed that th 3v3 cold side never touch 220v
CLK + JTAG + SCI
BOOTSRAP R's

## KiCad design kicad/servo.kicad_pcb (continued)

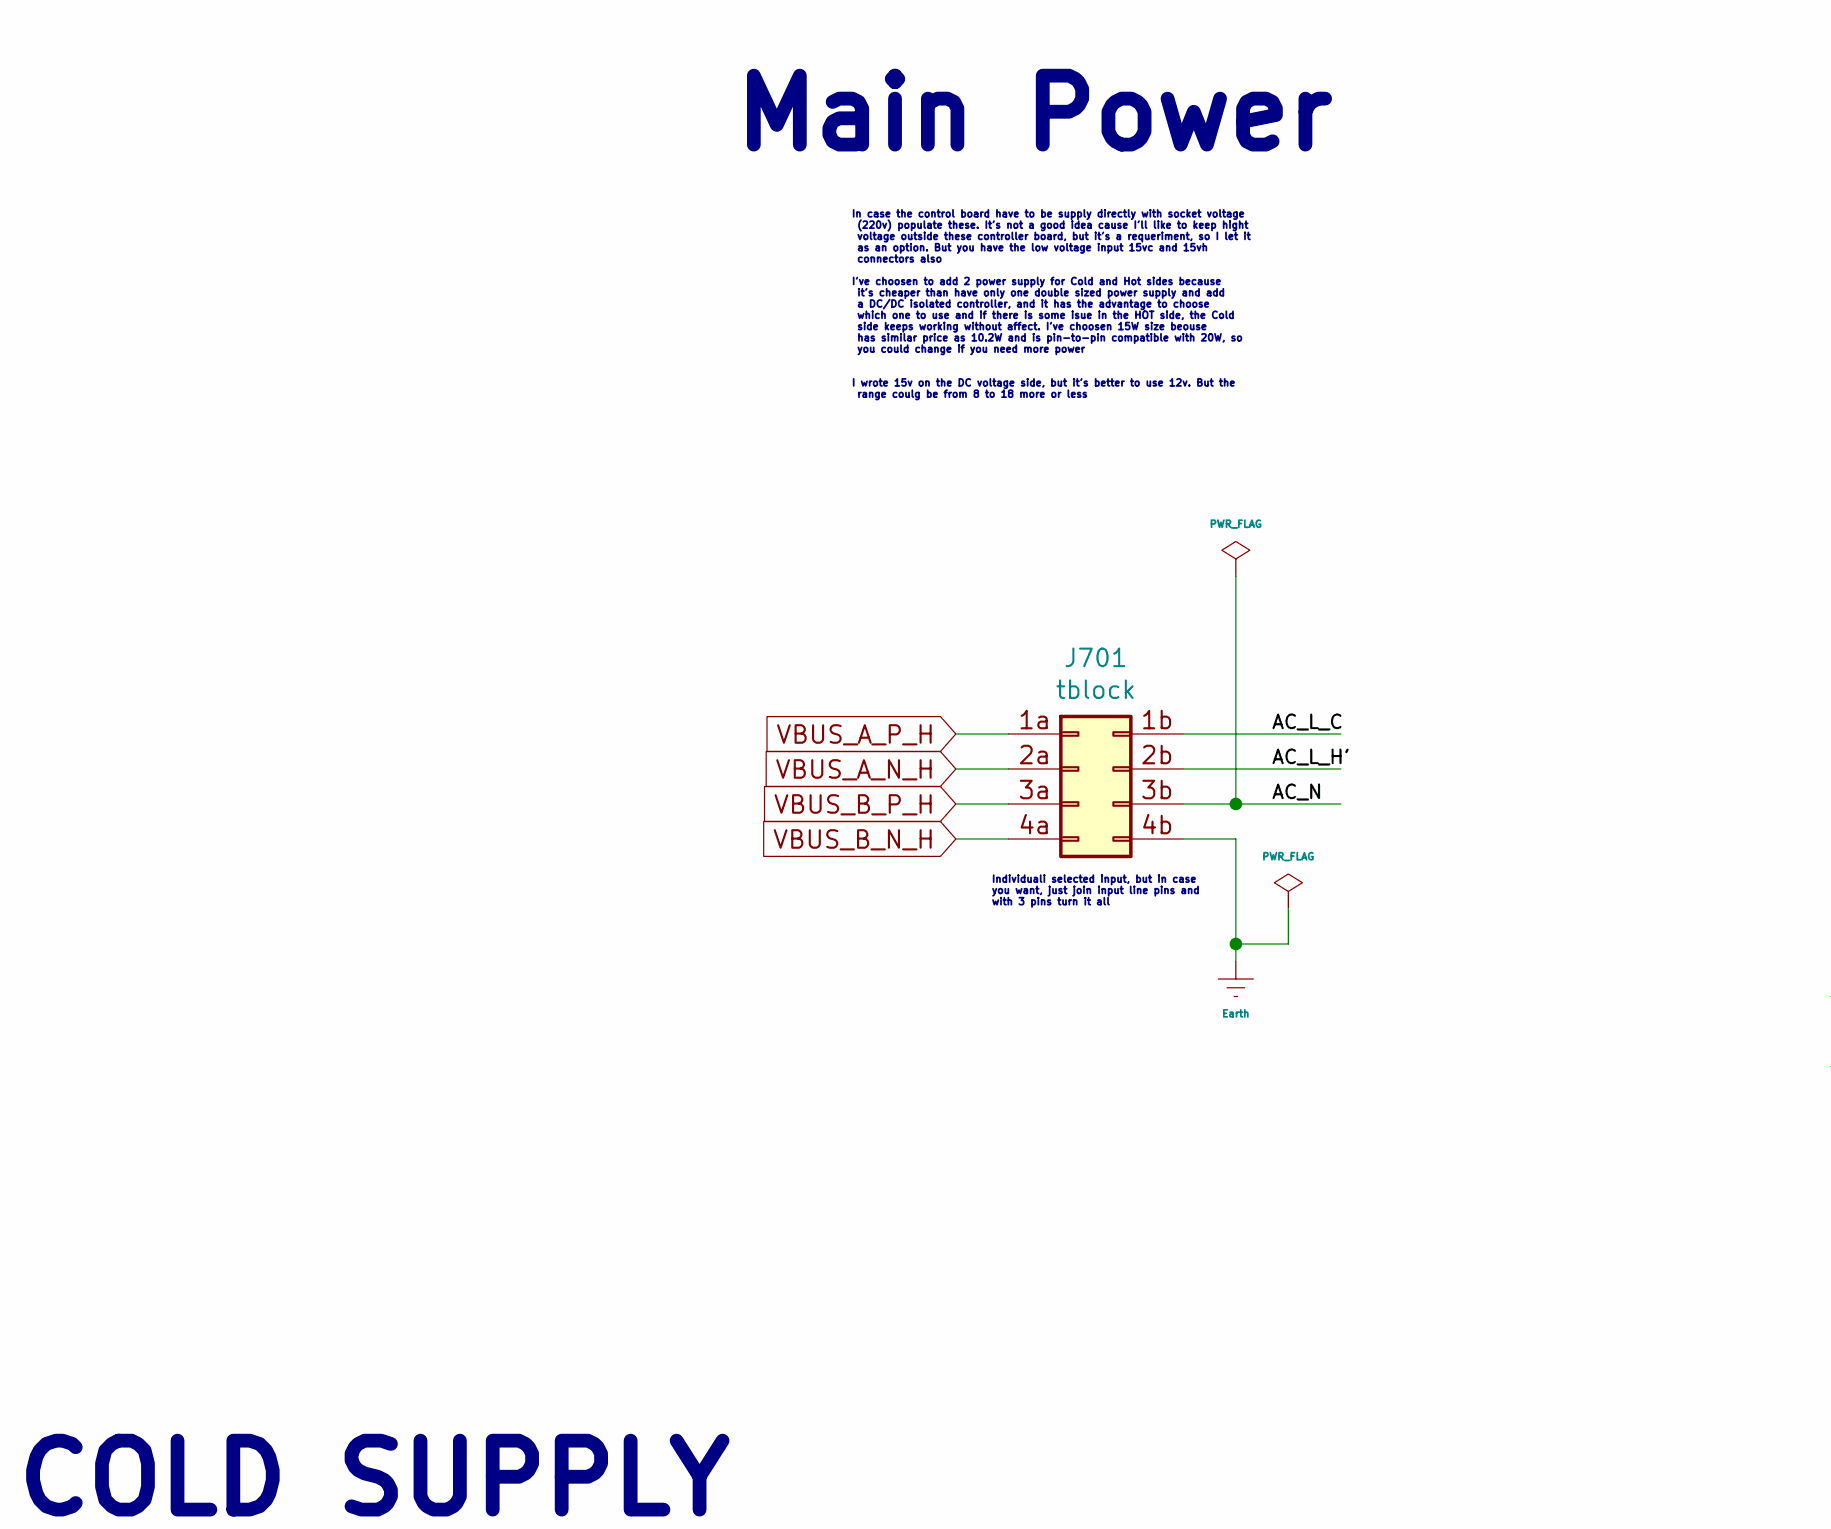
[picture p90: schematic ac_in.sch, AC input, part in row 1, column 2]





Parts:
C702: 220uF; C_0603_1608Metric
C703, C704, C708, C711, C712: 22uF; C_0603_1608Metric
C706, C707, C710, C713, C714: 100nF; C_0603_1608Metric
D701, D705: green; LED_0603_1608Metric
D702, D704: red; LED_0603_1608Metric
D706: blue; LED_0603_1608Metric
F701, F702: Fuse; fuse_3912
J701: tblock; tblock02x04
JP701, JP702: jumper; SolderJumper-2_P1.3mm_Open_RoundedPad1.0x1.5mm
PS701: IRM-10-5; Converter_ACDC_MeanWell_IRM-10-xx_THT
PS702: irm-10-12; Converter_ACDC_MeanWell_IRM-10-xx_THT
R701, R702, R704, R705, R706: 680; R_0603_1608Metric
U702: R-783.3-1.0; Converter_DCDC_RECOM_R-78E-0.5_THT
U704: R-78E5.0-1.0; Converter_DCDC_RECOM_R-78E-0.5_THT
U705, U706: AP2114H-1.2TRG1; SOT-223

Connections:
1V2C: C712.2 (Capacitor), C714.2 (Capacitor), R706.1, U706.2 (VOUT), U706.4 (VOUT); also elsewhere on the board
3V3: C711.2 (Capacitor), C713.2 (Capacitor), R705.1, U705.2 (VOUT), U705.4 (VOUT); also elsewhere on the board
5VC: C703.2 (Capacitor), C706.2 (Capacitor), JP701.2, U702.1 (IN), U705.3 (VIN); also elsewhere on the board
5VH: C708.2 (Capacitor), C710.2 (Capacitor), R704.1, U704.3 (OUT); also elsewhere on the board
15VH: C702.2 (Capacitor), JP702.2, U704.1 (IN); also elsewhere on the board
/ac_in/5VC_IN: JP701.1, PS701.4 (+Vout), R701.1
/ac_in/15VH_IN: JP702.1, PS702.4 (+Vout), R702.1
/ac_in/AC_L_C: F701.2, J701.1b
/ac_in/AC_L_H': F702.2, J701.2b
/ac_in/AC_N: J701.3b, PS701.2 (AC/N), PS702.2 (AC/N)
Earth: J701.4b; also elsewhere on the board
GND: C703.1, C704.1, C706.1, C707.1, C711.1, C712.1, C713.1, C714.1, D701.1 (K), D705.1 (K), D706.1 (K), PS701.3 (-Vout), U702.2 (GND), U705.1 (GND), U706.1 (GND); also elsewhere on the board
GNDH: C702.1, C708.1, C710.1, D702.1 (K), D704.1 (K), PS702.3 (-Vout), U704.2 (GND); also elsewhere on the board
unnamed: C704.2 (Capacitor), C707.2 (Capacitor), U702.3 (OUT), U706.3 (VIN)
unnamed: D701.2 (A), R701.2
unnamed: D702.2 (A), R702.2
unnamed: D704.2 (A), R704.2
unnamed: D705.2 (A), R705.2
unnamed: D706.2 (A), R706.2
unnamed: F701.1, PS701.1 (AC/L)
unnamed: F702.1, PS702.1 (AC/L)
VBUS_A_N_H: J701.2a; also elsewhere on the board
VBUS_A_P_H: J701.1a; also elsewhere on the board
VBUS_B_N_H: J701.4a; also elsewhere on the board
VBUS_B_P_H: J701.3a; also elsewhere on the board

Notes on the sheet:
in case we need more current use another 5v dc/dc and open jumper to no overload the previos schitching power supply. if not, just chain and do not place the extra 78E5
COLD SUPPLY
HOT SUPPLY
Main Power
Take in account that hot doesn't mean that it is refered to high voltage AC socket input path like 220v/380v. It is intended to isolate the uC /logic/user interfase side from accidentally high voltage contact on the hot side and prevent injuries as to make the reinforced isolation possible with one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
sip 3 package, cheap, easy to replace and many options
In case the control board have to be supply directly with socket voltage (220v) populate these. It's not a good idea cause I'll like to keep hight voltage outside these controller board, but it's a requeriment, so I let it as an option. But you have the low voltage input 15vc and 15vh connectors al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
It is inteded to use only, I mean ONLY inside the control board, none of these coopers wires has to leave the board. I isolate every single pin from these supply to go outside, take these in account
the intention of the LCD it to clean the noise without using big filters and L's. It's recommended and tested that these method works pretty low noise LDO <30uV
Individuali selected input, but in case you want, just join input line pins and with 3 pins turn it all

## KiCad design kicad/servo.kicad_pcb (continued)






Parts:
C801, C802, C803, C804, C805, C806, C807, C808, C809, C810, C811, C812, C813, C814, C815, C816, C817, C818, C819, C820, C821, C822, C823, C824: 10p; C_0603_1608Metric
C825, C826, C833, C834: 10u; C_0603_1608Metric
C827, C828, C829, C830, C831, C832, C835, C836, C837, C838, C839, C840, C841, C842: 0.1u; C_0603_1608Metric
R801, R802, R803, R804, R805, R806, R807, R808, R809, R810, R811, R812, R813, R814, R815, R816, R817, R818, R819, R820, R821, R822, R823, R824: 22e; R_0603_1608Metric
U801, U813: SI8660BD; SOIC-16W_7.5x10.3mm_P1.27mm
U802, U814: SI8662BD; SOIC-16W_7.5x10.3mm_P1.27mm
U803, U804, U805, U806, U807, U808, U809, U810, U811, U812: SN74LVC2G17DBVR; SOT-23-6

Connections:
3V3: C825.1, C826.1, C833.1, C834.1, U801.1 (VCC1), U802.1 (VCC1), U813.1 (VCC1), U814.1 (VCC1); also elsewhere on the board
5VH: C827.1, C828.1, C829.1, C830.1, C831.1, C832.1, C835.1, C836.1, C837.1, C838.1, C839.1, C840.1, C841.1, C842.1, U801.16 (VCC2), U802.16 (VCC2), U803.5 (VCC), U804.5 (VCC), U805.5 (VCC), U806.5 (VCC), U807.5 (VCC), U808.5 (VCC), U809.5 (VCC), U810.5 (VCC), U811.5 (VCC), U812.5 (VCC), U813.16 (VCC2), U814.16 (VCC2); also elsewhere on the board
BRK_A_MEC_C: U802.3 (A2); also elsewhere on the board
BRK_A_MEC_H: C805.2 (Capacitor), R808.2; also elsewhere on the board
BRK_B_MEC_C: U814.3 (A2); also elsewhere on the board
BRK_B_MEC_H: C820.2 (Capacitor), R820.1; also elsewhere on the board
FAN_RPM1: U802.6 (A5); also elsewhere on the board
FAN_RPM1_H: R811.2; also elsewhere on the board
FAN_RPM2: U814.6 (A5); also elsewhere on the board
FAN_RPM2_H: R823.1; also elsewhere on the board
FREE_OUT_A1: U802.4 (A3); also elsewhere on the board
FREE_OUT_A1_H: C804.2 (Capacitor), R809.2; also elsewhere on the board
FREE_OUT_A2: U802.5 (A4); also elsewhere on the board
FREE_OUT_A2_H: C803.2 (Capacitor), R810.2; also elsewhere on the board
FREE_OUT_B1: U814.4 (A3); also elsewhere on the board
FREE_OUT_B1_H: C821.2 (Capacitor), R821.1; also elsewhere on the board
FREE_OUT_B2: U814.5 (A4); also elsewhere on the board
FREE_OUT_B2_H: C822.2 (Capacitor), R822.1; also elsewhere on the board
GND: C825.2 (Capacitor), C826.2 (Capacitor), C833.2 (Capacitor), C834.2 (Capacitor), U801.8 (GND1), U802.8 (GND1), U813.8 (GND1), U814.8 (GND1); also elsewhere on the board
GNDH: C801.1, C802.1, C803.1, C804.1, C805.1, C806.1, C807.1, C808.1, C809.1, C810.1, C811.1, C812.1, C813.1, C814.1, C815.1, C816.1, C817.1, C818.1, C819.1, C820.1, C821.1, C822.1, C823.1, C824.1, C827.2 (Capacitor), C828.2 (Capacitor), C829.2 (Capacitor), C830.2 (Capacitor), C831.2 (Capacitor), C832.2 (Capacitor), C835.2 (Capacitor), C836.2 (Capacitor), C837.2 (Capacitor), C838.2 (Capacitor), C839.2 (Capacitor), C840.2 (Capacitor), C841.2 (Capacitor), C842.2 (Capacitor), U801.9 (GND2), U802.9 (GND2), U803.2 (GND), U804.2 (GND), U805.2 (GND), U806.2 (GND), U807.2 (GND), U808.2 (GND), U809.2 (GND), U810.2 (GND), U811.2 (GND), U812.2 (GND), U813.9 (GND2), U814.9 (GND2); also elsewhere on the board
IGBT_ALARM1: U802.7 (A6); also elsewhere on the board
IGBT_ALARM1_H: R812.2; also elsewhere on the board
IGBT_ALARM2: U814.7 (A6); also elsewhere on the board
IGBT_ALARM2_H: R824.1; also elsewhere on the board
unnamed: C801.2 (Capacitor), R812.1, U802.10 (B6)
unnamed: C802.2 (Capacitor), R811.1, U802.11 (B5)
unnamed: C823.2 (Capacitor), R823.2, U814.11 (B5)
unnamed: C824.2 (Capacitor), R824.2, U814.10 (B6)
unnamed: R801.1, U803.6 (1Y)
unnamed: R802.1, U803.4 (2Y)
unnamed: R803.1, U804.6 (1Y)
unnamed: R804.1, U804.4 (2Y)
unnamed: R805.1, U805.6 (1Y)
unnamed: R806.1, U805.4 (2Y)
unnamed: R807.1, U806.6 (1Y)
unnamed: R808.1, U806.4 (2Y)
unnamed: R809.1, U807.6 (1Y)
unnamed: R810.1, U807.4 (2Y)
unnamed: R813.2, U808.6 (1Y)
unnamed: R814.2, U808.4 (2Y)
unnamed: R815.2, U809.6 (1Y)
unnamed: R816.2, U809.4 (2Y)
unnamed: R817.2, U810.6 (1Y)
unnamed: R818.2, U810.4 (2Y)
unnamed: R819.2, U811.6 (1Y)
unnamed: R820.2, U811.4 (2Y)
unnamed: R821.2, U812.6 (1Y)
unnamed: R822.2, U812.4 (2Y)
unnamed: U801.10 (B6), U805.3 (2A)
unnamed: U801.11 (B5), U805.1 (1A)
unnamed: U801.12 (B4), U804.3 (2A)
unnamed: U801.13 (B3), U804.1 (1A)
unnamed: U801.14 (B2), U803.3 (2A)
unnamed: U801.15 (B1), U803.1 (1A)
unnamed: U802.12 (B4), U807.3 (2A)
unnamed: U802.13 (B3), U807.1 (1A)
unnamed: U802.14 (B2), U806.3 (2A)
unnamed: U802.15 (B1), U806.1 (1A)
unnamed: U808.1 (1A), U813.15 (B1)
unnamed: U808.3 (2A), U813.14 (B2)
unnamed: U809.1 (1A), U813.13 (B3)
unnamed: U809.3 (2A), U813.12 (B4)
unnamed: U810.1 (1A), U813.11 (B5)
unnamed: U810.3 (2A), U813.10 (B6)
unnamed: U811.1 (1A), U814.15 (B1)
unnamed: U811.3 (2A), U814.14 (B2)
unnamed: U812.1 (1A), U814.13 (B3)
unnamed: U812.3 (2A), U814.12 (B4)
PWM_A_1H_C: U801.2 (A1); also elsewhere on the board
PWM_A_1H_H: C818.2 (Capacitor), R801.2; also elsewhere on the board
PWM_A_1L_C: U801.3 (A2); also elsewhere on the board
PWM_A_1L_H: C816.2 (Capacitor), R802.2; also elsewhere on the board
PWM_A_2H_C: U801.4 (A3); also elsewhere on the board
PWM_A_2H_H: C814.2 (Capacitor), R803.2; also elsewhere on the board
PWM_A_2L_C: U801.5 (A4); also elsewhere on the board
PWM_A_2L_H: C812.2 (Capacitor), R804.2; also elsewhere on the board
PWM_A_3H_C: U801.6 (A5); also elsewhere on the board
PWM_A_3H_H: C810.2 (Capacitor), R805.2; also elsewhere on the board
PWM_A_3L_C: U801.7 (A6); also elsewhere on the board
PWM_A_3L_H: C808.2 (Capacitor), R806.2; also elsewhere on the board
PWM_A_BRK_RES_C: U802.2 (A1); also elsewhere on the board
PWM_A_BRK_RES_H: C806.2 (Capacitor), R807.2; also elsewhere on the board
PWM_B_1H_C: U813.2 (A1); also elsewhere on the board
PWM_B_1H_H: C807.2 (Capacitor), R813.1; also elsewhere on the board
PWM_B_1L_C: U813.3 (A2); also elsewhere on the board
PWM_B_1L_H: C809.2 (Capacitor), R814.1; also elsewhere on the board
PWM_B_2H_C: U813.4 (A3); also elsewhere on the board
PWM_B_2H_H: C811.2 (Capacitor), R815.1; also elsewhere on the board
PWM_B_2L_C: U813.5 (A4); also elsewhere on the board
PWM_B_2L_H: C813.2 (Capacitor), R816.1; also elsewhere on the board
PWM_B_3H_C: U813.6 (A5); also elsewhere on the board
PWM_B_3H_H: C815.2 (Capacitor), R817.1; also elsewhere on the board
PWM_B_3L_C: U813.7 (A6); also elsewhere on the board
PWM_B_3L_H: C817.2 (Capacitor), R818.1; also elsewhere on the board
PWM_B_BRK_RES_C: U814.2 (A1); also elsewhere on the board
PWM_B_BRK_RES_H: C819.2 (Capacitor), R819.1; also elsewhere on the board

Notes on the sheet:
PWM OUT -> ISOLATOR -> BUFFER -> FILTER
these pins has isolation and a buffer. They could be directly connected to a IGBT module for test porpouses or to a power board and another isolation stage for production porpouses to have a reinforced isolation. In next stages of the development of the board, the buffers could be eliminated, but n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
Choose a package pin-to-pin compatible with TI ISO7760. But SIlabs cost halt the price as TI
Free to other uses. If oyu choose another version of these IC that has some pins reverted to input, you could use these as an isolated general input also, just remember to bridge the output buffer or reverse it also

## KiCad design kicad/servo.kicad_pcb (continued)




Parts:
C901, C902, C915, C916: 1nF; C_0603_1608Metric
C903, C904, C905, C906, C907, C908, C909, C910, C911, C912, C913, C914, C917, C918: 100nF; C_0603_1608Metric
R901, R902, R903, R904, R907, R920, R921, R922, R923: 2k2; R_0603_1608Metric
R905, R906, R918, R919: 12e; R_0603_1608Metric
R908: 120e NP; R_0603_1608Metric
R909, R911, R913, R915, R917: 10k; R_0603_1608Metric
R910, R912, R914, R916: 1k(dnp); R_0603_1608Metric
U901, U902, U904, U905: AMC1311B; SSO-8_9.6x6.3mm_P1.27mm_Clearance10.5mm
U903: ADM2483; SOIC-16W_7.5x10.3mm_P1.27mm

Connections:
1-WIREN_H: R908.2, R909.1, U903.13 (B); also elsewhere on the board
1-WIREP_H: R907.2, R908.1, U903.12 (A); also elsewhere on the board
1Wire_EN: U903.4 (~RE), U903.5 (DE); also elsewhere on the board
1Wire_IN: U903.3 (RxD); also elsewhere on the board
1Wire_OUT: U903.6 (TxD); also elsewhere on the board
3V3: C903.2 (Capacitor), C904.2 (Capacitor), C913.2 (Capacitor), C914.2 (Capacitor), C917.2 (Capacitor), U901.8 (VDD2), U902.8 (VDD2), U903.1 (VDD1), U903.7 (PV), U904.8 (VDD2), U905.8 (VDD2); also elsewhere on the board
5VH: C905.2 (Capacitor), C906.2 (Capacitor), C911.2 (Capacitor), C912.2 (Capacitor), C918.2 (Capacitor), R907.1, R910.1, R912.1, R914.1, R916.1, U901.1 (VDD1), U902.1 (VDD1), U903.16 (VDD2), U904.1 (VDD1), U905.1 (VDD1); also elsewhere on the board
GND: C903.1, C904.1, C913.1, C914.1, C917.1, U901.5 (GND2), U902.5 (GND2), U903.2 (GND1), U903.8 (GND1), U904.5 (GND2), U905.5 (GND2); also elsewhere on the board
GNDH: C905.1, C906.1, C907.1, C908.1, C909.1, C910.1, C911.1, C912.1, C918.1, R909.2, R911.2, R913.2, R915.2, R917.2, U901.3 (SHTDN), U901.4 (GND1), U902.3 (SHTDN), U902.4 (GND1), U903.9 (GND2), U903.15 (GND2), U904.3 (SHTDN), U904.4 (GND1), U905.3 (SHTDN), U905.4 (GND1); also elsewhere on the board
NTCA1_H: R905.2, R910.2, R911.1; also elsewhere on the board
NTCA1_N: C901.1, R902.2; also elsewhere on the board
NTCA1_P: C901.2 (Capacitor), R901.2; also elsewhere on the board
NTCA2_H: R906.2, R912.2, R913.1; also elsewhere on the board
NTCA2_N: C902.1, R904.2; also elsewhere on the board
NTCA2_P: C902.2 (Capacitor), R903.2; also elsewhere on the board
NTCB1_H: R914.2, R915.1, R918.2; also elsewhere on the board
NTCB1_N: C915.1, R921.2; also elsewhere on the board
NTCB1_P: C915.2 (Capacitor), R920.2; also elsewhere on the board
NTCB2_H: R916.2, R917.1, R919.2; also elsewhere on the board
NTCB2_N: C916.1, R923.2; also elsewhere on the board
NTCB2_P: C916.2 (Capacitor), R922.2; also elsewhere on the board
unnamed: C907.2 (Capacitor), R905.1, U901.2 (VIN_P)
unnamed: C908.2 (Capacitor), R906.1, U902.2 (VIN_P)
unnamed: C909.2 (Capacitor), R918.1, U904.2 (VIN_P)
unnamed: C910.2 (Capacitor), R919.1, U905.2 (VIN_P)
unnamed: R901.1, U901.7 (VOUT_P)
unnamed: R902.1, U901.6 (VOUT_N)
unnamed: R903.1, U902.7 (VOUT_P)
unnamed: R904.1, U902.6 (VOUT_N)
unnamed: R920.1, U904.7 (VOUT_P)
unnamed: R921.1, U904.6 (VOUT_N)
unnamed: R922.1, U905.7 (VOUT_P)
unnamed: R923.1, U905.6 (VOUT_N)

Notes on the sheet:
Could be used by isolated: 485, 1-wire bus, general IO pin You could choose between 15b or 5v(default) output using a soldering jumper
2 isolated NTC interfase + 1 isolated 1-wire/485
it;d be used as a voltage sensor, pullup/pulldown'ded NTC measurement, or general input aquire
I left 2 isolated analog input to measure until 2 NTC for each motor. If each motor has one inside the motor and other for IGBT disipator, If you need more precisiion or more sensors, I left also an isolated 1-wire/RS485 interfase that could manage a lot of 18B20 on a bus network.


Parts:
C1001: 100nF; C_0603_1608Metric
J1001: tblock2x6; tblock02x6_3.81
JP1001: jumper; SolderJumper-3_P1.3mm_Open_RoundedPad1.0x1.5mm
R1001, R1003, R1004, R1006, R1007, R1009, R1010, R1012: 10k; R_0603_1608Metric
R1002, R1005, R1008, R1011: 1k; R_0603_1608Metric
U1001: am26ls32a; SOIC-16W_5.3x10.2mm_P1.27mm

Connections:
5VH: C1001.2 (Capacitor), JP1001.1 (A), R1001.1, R1004.1, R1007.1, R1010.1, U1001.4 (EN), U1001.16 (VDD); also elsewhere on the board
15VH: JP1001.3 (B); also elsewhere on the board
/step_dir/STEP1_A+_H: J1001.2a, R1001.2, R1002.1, U1001.6 (A2)
/step_dir/STEP1_A-_H: J1001.3a, R1002.2, R1003.1, U1001.7 (B2)
/step_dir/STEP1_B+_H: J1001.4a, R1004.2, R1005.1, U1001.2 (A1)
/step_dir/STEP1_B-_H: J1001.5a, R1005.2, R1006.1, U1001.1 (B1)
/step_dir/STEP2_A+_H: J1001.2b, R1010.2, R1011.1, U1001.14 (A4)
/step_dir/STEP2_A-_H: J1001.3b, R1011.2, R1012.1, U1001.15 (B4)
/step_dir/STEP2_B+_H: J1001.4b, R1007.2, R1008.1, U1001.10 (A3)
/step_dir/STEP2_B-_H: J1001.5b, R1008.2, R1009.1, U1001.9 (B3)
DIR1_H: U1001.5 (Out2); also elsewhere on the board
DIR2_H: U1001.11 (Out3); also elsewhere on the board
GNDH: C1001.1, J1001.6a, J1001.6b, R1003.2, R1006.2, R1009.2, R1012.2, U1001.8 (GND), U1001.12 (~EN); also elsewhere on the board
unnamed: J1001.1a, J1001.1b, JP1001.2 (C)
STEP1_H: U1001.3 (Out1); also elsewhere on the board
STEP2_H: U1001.13 (Out4); also elsewhere on the board

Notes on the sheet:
Differential STEP-DIR input HOT
optional one to hi or/and one to low
The isolation part is shared with QEP

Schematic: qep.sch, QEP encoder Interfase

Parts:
C1101, C1102, C1103, C1104, C1105, C1106: 100nF; C_0603_1608Metric
J1101: tblock; tblock02x10_3.81
JP1101: jumper; SolderJumper-3_P1.3mm_Open_RoundedPad1.0x1.5mm
R1101, R1103, R1104, R1106, R1107, R1109, R1110, R1112, R1113, R1115, R1116, R1118, R1119, R1121, R1122, R1124: 10k; R_0603_1608Metric
R1102, R1105, R1108, R1111, R1114, R1117, R1120, R1123: 1k; R_0603_1608Metric
U1101, U1104: SI8660BD; SOIC-16W_7.5x10.3mm_P1.27mm
U1102, U1103: am26ls32a; SOIC-16W_5.3x10.2mm_P1.27mm

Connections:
3V3: C1101.2 (Capacitor), C1106.2 (Capacitor), U1101.16 (VCC2), U1104.16 (VCC2); also elsewhere on the board
5VH: C1102.2 (Capacitor), C1103.2 (Capacitor), C1104.2 (Capacitor), C1105.2 (Capacitor), JP1101.1 (A), R1101.1, R1104.1, R1107.1, R1110.1, R1113.1, R1116.1, R1119.1, R1122.1, U1101.1 (VCC1), U1102.4 (EN), U1102.16 (VDD), U1103.4 (EN), U1103.16 (VDD), U1104.1 (VCC1); also elsewhere on the board
15VH: JP1101.3 (B); also elsewhere on the board
/qep/QEP1_A+_H: J1101.2a, R1101.2, R1102.1, U1102.2 (A1)
/qep/QEP1_A-_H: J1101.3a, R1102.2, R1103.1, U1102.1 (B1)
/qep/QEP1_B+_H: J1101.4a, R1104.2, R1105.1, U1102.6 (A2)
/qep/QEP1_B-_H: J1101.5a, R1105.2, R1106.1, U1102.7 (B2)
/qep/QEP1_I+_H: J1101.6a, R1107.2, R1108.1, U1102.10 (A3)
/qep/QEP1_I-_H: J1101.7a, R1108.2, R1109.1, U1102.9 (B3)
/qep/QEP1_S+_H: J1101.8a, R1110.2, R1111.1, U1102.14 (A4)
/qep/QEP1_S-_H: J1101.9a, R1111.2, R1112.1, U1102.15 (B4)
/qep/QEP2_A+_H: J1101.2b, R1122.2, R1123.1, U1103.2 (A1)
/qep/QEP2_A-_H: J1101.3b, R1123.2, R1124.1, U1103.1 (B1)
/qep/QEP2_B+_H: J1101.4b, R1119.2, R1120.1, U1103.6 (A2)
/qep/QEP2_B-_H: J1101.5b, R1120.2, R1121.1, U1103.7 (B2)
/qep/QEP2_I+_H: J1101.6b, R1116.2, R1117.1, U1103.10 (A3)
/qep/QEP2_I-_H: J1101.7b, R1117.2, R1118.1, U1103.9 (B3)
/qep/QEP2_S+_H: J1101.8b, R1113.2, R1114.1, U1103.14 (A4)
/qep/QEP2_S-_H: J1101.9b, R1114.2, R1115.1, U1103.15 (B4)
DIR1: U1101.10 (B6); also elsewhere on the board
DIR1_H: U1101.7 (A6); also elsewhere on the board
DIR2: U1104.10 (B6); also elsewhere on the board
DIR2_H: U1104.7 (A6); also elsewhere on the board
GND: C1101.1, C1106.1, U1101.9 (GND2), U1104.9 (GND2); also elsewhere on the board
GNDH: C1102.1, C1103.1, C1104.1, C1105.1, J1101.10a, J1101.10b, R1103.2, R1106.2, R1109.2, R1112.2, R1115.2, R1118.2, R1121.2, R1124.2, U1101.8 (GND1), U1102.8 (GND), U1102.12 (~EN), U1103.8 (GND), U1103.12 (~EN), U1104.8 (GND1); also elsewhere on the board
unnamed: J1101.1a, J1101.1b, JP1101.2 (C)
unnamed: U1101.2 (A1), U1102.3 (Out1)
unnamed: U1101.3 (A2), U1102.5 (Out2)
unnamed: U1101.4 (A3), U1102.11 (Out3)
unnamed: U1101.5 (A4), U1102.13 (Out4)
unnamed: U1103.3 (Out1), U1104.2 (A1)
unnamed: U1103.5 (Out2), U1104.3 (A2)
unnamed: U1103.11 (Out3), U1104.4 (A3)
unnamed: U1103.13 (Out4), U1104.5 (A4)
QEP1_A: U1101.15 (B1); also elsewhere on the board
QEP1_B: U1101.14 (B2); also elsewhere on the board
QEP1_I: U1101.13 (B3); also elsewhere on the board
QEP1_S: U1101.12 (B4); also elsewhere on the board
QEP2_A: U1104.15 (B1); also elsewhere on the board
QEP2_B: U1104.14 (B2); also elsewhere on the board
QEP2_I: U1104.13 (B3); also elsewhere on the board
QEP2_S: U1104.12 (B4); also elsewhere on the board
STEP1: U1101.11 (B5); also elsewhere on the board
STEP1_H: U1101.6 (A5); also elsewhere on the board
STEP2: U1104.11 (B5); also elsewhere on the board
STEP2_H: U1104.6 (A5); also elsewhere on the board

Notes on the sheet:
2x Isolated Idifferential ncremental encoder interfase 5v input A-B-I-S
I left the input for two isolated incremental encoders. I left the 4 signals input plus two auxiliary output for eny porpous plus the ability to choose between 5 or 15vH
optional one to hi or/and one to low
Choose a package pin-to-pin compatible with TI ISO7760. But SIlabs cost halt the price as TI

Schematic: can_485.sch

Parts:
C1201, C1202, C1203, C1204: 100nF; C_0603_1608Metric
J1201: tblock2x4; tblock02x4_3.81
JP1201, JP1202: jumper; SolderJumper-3_P1.3mm_Open_RoundedPad1.0x1.5mm
R1201, R1203, R1204, R1206: 10k; R_0603_1608Metric
R1202, R1205: 1k; R_0603_1608Metric
U1201: ISO1050; SSO-8_6.7x9.8mm_P2.54mm_Clearance8mm
U1202: ADM2483; SOIC-16W_7.5x10.3mm_P1.27mm

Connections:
3V3: C1201.2 (Capacitor), C1204.2 (Capacitor), U1201.1 (VCC1), U1202.1 (VDD1), U1202.7 (PV); also elsewhere on the board
5VH: C1202.2 (Capacitor), C1203.2 (Capacitor), JP1201.1 (A), R1201.1, R1204.1, U1201.8 (VCC2), U1202.16 (VDD2); also elsewhere on the board
15VH: JP1201.3 (B); also elsewhere on the board
CAN_RX: U1201.2 (RxD); also elsewhere on the board
CAN_TX: U1201.3 (TxD); also elsewhere on the board
Earth: JP1202.1 (A); also elsewhere on the board
GND: C1201.1, C1204.1, U1201.4 (GND1), U1202.2 (GND1), U1202.8 (GND1); also elsewhere on the board
GNDH: C1202.1, C1203.1, JP1202.3 (B), R1203.2, R1206.2, U1201.5 (GND2), U1202.9 (GND2), U1202.15 (GND2); also elsewhere on the board
unnamed: J1201.1a, J1201.1b, JP1201.2 (C)
unnamed: J1201.2a, R1201.2, R1202.1, U1201.7 (CANH)
unnamed: J1201.2b, R1204.2, R1205.1, U1202.12 (A)
unnamed: J1201.3a, R1202.2, R1203.1, U1201.6 (CANL)
unnamed: J1201.3b, R1205.2, R1206.1, U1202.13 (B)
unnamed: J1201.4a, J1201.4b, JP1202.2 (C)
RS485_EN: U1202.4 (~RE), U1202.5 (DE); also elsewhere on the board
RS485_RX: U1202.3 (RxD); also elsewhere on the board
RS485_TX: U1202.6 (TxD); also elsewhere on the board

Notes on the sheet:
Isolated CAN interfase
A simple CAN driver. It also could be used as a RS485 driver in his speed.. the minimum for CAN is 40kbos, so in RS485 at 9600 could be fine
Could be used by isolated: 485, 1-wire bus, general IO pin
Isolated RS485
With these interfase you could manage isolated RS485 or isolated GPIO or isolated 1-Wire, using 5H or 15H as a supply

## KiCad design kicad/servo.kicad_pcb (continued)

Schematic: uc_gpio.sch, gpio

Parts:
U301: TMS320F28388DZWTS; BGA337CP80_19X19_1600X1600X140B50N; PartNumber TMS320F28388DZWTS

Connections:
1Wire_EN: U301.B14 (GPIO82); also elsewhere on the board
1Wire_IN: U301.A14 (GPIO81); also elsewhere on the board
1Wire_OUT: U301.C14 (GPIO83); also elsewhere on the board
BOOT1: U301.B16 (GPIO72); also elsewhere on the board
BOOT2: U301.A11 (GPIO84); also elsewhere on the board
BRK_A_MEC_C: U301.U13 (GPIO32); also elsewhere on the board
BRK_B_MEC_C: U301.T13 (GPIO33); also elsewhere on the board
CAN_RX: U301.T11 (GPIO30/CANA_RX); also elsewhere on the board
CAN_TX: U301.U11 (GPIO31/CANA_TX); also elsewhere on the board
DIR1: U301.C18 (GPIO68); also elsewhere on the board
DIR2: U301.A17 (GPIO70); also elsewhere on the board
ECAT0_RJ_LED0: U301.F18 (GPIO143/ESC_LED_LINK0_ACTIVE); also elsewhere on the board
ECAT0_RJ_LED1: U301.D14 (GPIO148/ESC_PHY0_LINKSTATUS); also elsewhere on the board
ECAT0_RX_CLK: U301.A8 (GPIO163/ESC_RX0_CLK); also elsewhere on the board
ECAT0_RX_D0: U301.C5 (GPIO165/ESC_RX0_DATA0); also elsewhere on the board
ECAT0_RX_D1: U301.D5 (GPIO166/ESC_RX0_DATA1); also elsewhere on the board
ECAT0_RX_D2: U301.C4 (GPIO167/ESC_RX0_DATA2); also elsewhere on the board
ECAT0_RX_D3: U301.D4 (GPIO168/ESC_RX0_DATA3); also elsewhere on the board
ECAT0_RX_DV: U301.D9 (GPIO162/ESC_RX0_DV); also elsewhere on the board
ECAT0_RX_ER: U301.B8 (GPIO164/ESC_RX0_ERR); also elsewhere on the board
ECAT0_TX_CLK: U301.B10 (GPIO157/ESC_TX0_CLK); also elsewhere on the board
ECAT0_TX_D0: U301.C10 (GPIO158/ESC_TX0_DATA0); also elsewhere on the board
ECAT0_TX_D1: U301.D10 (GPIO159/ESC_TX0_DATA1); also elsewhere on the board
ECAT0_TX_D2: U301.B9 (GPIO160/ESC_TX0_DATA2); also elsewhere on the board
ECAT0_TX_D3: U301.C9 (GPIO161/ESC_TX0_DATA3); also elsewhere on the board
ECAT0_TX_EN: U301.D12 (GPIO156/ESC_TX0_ENA); also elsewhere on the board
ECAT1_RJ_LED0: U301.F17 (GPIO144/ESC_LED_LINK1_ACTIVE); also elsewhere on the board
ECAT1_RJ_LED1: U301.A13 (GPIO149/ESC_PHY1_LINKSTATUS); also elsewhere on the board
ECAT1_RX_CLK: U301.T18 (GPIO137); also elsewhere on the board
ECAT1_RX_D0: U301.N19 (GPIO139); also elsewhere on the board
ECAT1_RX_D1: U301.M19 (GPIO140); also elsewhere on the board
ECAT1_RX_D2: U301.M18 (GPIO141); also elsewhere on the board
ECAT1_RX_D3: U301.L19 (GPIO142); also elsewhere on the board
ECAT1_RX_DV: U301.T17 (GPIO136); also elsewhere on the board
ECAT1_RX_ER: U301.T19 (GPIO138); also elsewhere on the board
ECAT1_TX_CLK: U301.U10 (GPIO130); also elsewhere on the board
ECAT1_TX_D0: U301.V10 (GPIO131); also elsewhere on the board
ECAT1_TX_D1: U301.W18 (GPIO132); also elsewhere on the board
ECAT1_TX_D2: U301.V18 (GPIO134); also elsewhere on the board
ECAT1_TX_D3: U301.U18 (GPIO135); also elsewhere on the board
ECAT1_TX_EN: U301.T10 (GPIO129); also elsewhere on the board
ECAT_EEPROM_SCL: U301.C13 (GPIO151/ESC_I2C_SCL); also elsewhere on the board
ECAT_EEPROM_SDA: U301.B13 (GPIO150/ESC_I2C_SDA); also elsewhere on the board
ECAT_LED_ERR: U301.E17 (GPIO145/ESC_LED_ERR); also elsewhere on the board
ECAT_LED_RUN: U301.D18 (GPIO146/ESC_LED_RUN); also elsewhere on the board
ECAT_MDCLK: U301.D13 (GPIO152/ESC_MDIO_CLK); also elsewhere on the board
ECAT_MDIO: U301.A12 (GPIO153/ESC_MDIO_DATA); also elsewhere on the board
ECAT_RST: U301.C12 (GPIO155/ESC_PHY_RESETn); also elsewhere on the board
ENDAT1_CLK: U301.M17 (GPIO60/SPIA_CLK); also elsewhere on the board
ENDAT1_CS: U301.L16 (GPIO61/SPIA_STEn); also elsewhere on the board
ENDAT1_MISO: U301.M16 (GPIO59/SPIA_SOMI); also elsewhere on the board
ENDAT1_MOSI: U301.N17 (GPIO58/SPIA_SIMO); also elsewhere on the board
ENDAT1_N_SKEW_CLK: U301.D2 (GPIO14/EPWM8A); also elsewhere on the board
ENDAT1_Y_SKEW_CLK: U301.D3 (GPIO15/EPWM8B); also elsewhere on the board
ENDAT2_CLK: U301.K16 (GPIO65/SPIB_CLK); also elsewhere on the board
ENDAT2_CS: U301.K17 (GPIO66/SPIB_STEn); also elsewhere on the board
ENDAT2_MISO: U301.L17 (GPIO64/SPIB_SOMI); also elsewhere on the board
ENDAT2_MOSI: U301.J16 (GPIO63/SPIB_SIMO); also elsewhere on the board
ENDAT2_N_SKEW_CLK: U301.E3 (GPIO18/EPWM10A); also elsewhere on the board
ENDAT2_Y_SKEW_CLK: U301.E4 (GPIO19/EPWM10B); also elsewhere on the board
ENET_CAT_XI: U301.B12 (GPIO154/ESC_PHY_CLK); also elsewhere on the board
ENET_COL: U301.M2 (GPIO110); also elsewhere on the board
ENET_CRS: U301.N2 (GPIO109); also elsewhere on the board
ENET_MDCLK: U301.J3 (GPIO105); also elsewhere on the board
ENET_MDIO: U301.L2 (GPIO106); also elsewhere on the board
ENET_PWDN: U301.L4 (GPIO108); also elsewhere on the board
ENET_RST: U301.T15 (GPIO119); also elsewhere on the board
ENET_RX_CLK: U301.M4 (GPIO111); also elsewhere on the board
ENET_RX_D0: U301.N3 (GPIO114); also elsewhere on the board
ENET_RX_D1: U301.V12 (GPIO115); also elsewhere on the board
ENET_RX_D2: U301.W10 (GPIO116); also elsewhere on the board
ENET_RX_D3: U301.U12 (GPIO117); also elsewhere on the board
ENET_RX_DV: U301.M3 (GPIO112); also elsewhere on the board
ENET_RX_ER: U301.N4 (GPIO113); also elsewhere on the board
ENET_TX_CLK: U301.U15 (GPIO120); also elsewhere on the board
ENET_TX_D0: U301.W16 (GPIO121); also elsewhere on the board
ENET_TX_D1: U301.T8 (GPIO122); also elsewhere on the board
ENET_TX_D2: U301.U8 (GPIO123); also elsewhere on the board
ENET_TX_D3: U301.V8 (GPIO124); also elsewhere on the board
ENET_TX_EN: U301.T12 (GPIO118); also elsewhere on the board
FAN_RPM1: U301.K18 (GPIO44); also elsewhere on the board
FAN_RPM2: U301.R16 (GPIO48); also elsewhere on the board
FLASH_SPI_CLK: U301.H3 (GPIO102/SPIC_CLK); also elsewhere on the board
FLASH_SPI_CS: U301.J1 (GPIO103/SPIC_STEn); also elsewhere on the board
FLASH_SPI_MISO: U301.H2 (GPIO101/SPIC_SOMI); also elsewhere on the board
FLASH_SPI_MOSI: U301.H1 (GPIO100/SPIC_SIMO); also elsewhere on the board
FREE_OUT_A1: U301.V17 (GPIO40); also elsewhere on the board
FREE_OUT_A2: U301.U17 (GPIO41); also elsewhere on the board
FREE_OUT_B1: U301.E19 (GPIO46); also elsewhere on the board
FREE_OUT_B2: U301.E18 (GPIO47); also elsewhere on the board
IGBT_ALARM1: U301.K19 (GPIO45); also elsewhere on the board
IGBT_ALARM2: U301.P17 (GPIO53); also elsewhere on the board
LCD_GPIO0: U301.C6 (GPIO88); also elsewhere on the board
LCD_GPIO1: U301.D11 (GPIO87); also elsewhere on the board
LCD_GPIO2: U301.C11 (GPIO86); also elsewhere on the board
LCD_GPIO3: U301.B11 (GPIO85); also elsewhere on the board
LCD_GPIO4: U301.B3 (GPIO95); also elsewhere on the board
LCD_GPIO5: U301.C3 (GPIO96); also elsewhere on the board
LCD_INT: U301.A5 (GPIO90); also elsewhere on the board
LCD_SPI_CLK: U301.B4 (GPIO93/SPID_CLK); also elsewhere on the board
LCD_SPI_CS: U301.A3 (GPIO94/SPID_STEn); also elsewhere on the board
LCD_SPI_MISO: U301.A4 (GPIO92/SPID_SOMI); also elsewhere on the board
LCD_SPI_MOSI: U301.B5 (GPIO91/SPID_SIMO); also elsewhere on the board
LCD_SPI_PDW: U301.D6 (GPIO89); also elsewhere on the board
PWM4SD_CLK: U301.E1 (GPIO16/EPWM9A); also elsewhere on the board
PWM_A_1H_C: U301.C8 (GPIO0/EPWM1A); also elsewhere on the board
PWM_A_1L_C: U301.D8 (GPIO1/EPWM1A); also elsewhere on the board
PWM_A_2H_C: U301.A7 (GPIO2/EPWM2A); also elsewhere on the board
PWM_A_2L_C: U301.B7 (GPIO3/EPWM2B); also elsewhere on the board
PWM_A_3H_C: U301.C7 (GPIO4/EPWM3A); also elsewhere on the board
PWM_A_3L_C: U301.D7 (GPIO5/EPWM3B); also elsewhere on the board
PWM_A_BRK_RES_C: U301.C2 (GPIO12/EPWM7A); also elsewhere on the board
PWM_B_1H_C: U301.A6 (GPIO6/EPWM4A); also elsewhere on the board
PWM_B_1L_C: U301.B6 (GPIO7/EPWM4B); also elsewhere on the board
PWM_B_2H_C: U301.G2 (GPIO8/EPWM5A); also elsewhere on the board
PWM_B_2L_C: U301.G3 (GPIO9/EPWM5B); also elsewhere on the board
PWM_B_3H_C: U301.B2 (GPIO10/EPWM6A); also elsewhere on the board
PWM_B_3L_C: U301.C1 (GPIO11/EPWM6B); also elsewhere on the board
PWM_B_BRK_RES_C: U301.D1 (GPIO13/EPWM7B); also elsewhere on the board
QEP1_A: U301.F2 (GPIO20/EQEP1_A); also elsewhere on the board
QEP1_B: U301.F3 (GPIO21/EQEP1_B); also elsewhere on the board
QEP1_I: U301.K4 (GPIO23/EQEP1_INDEX); also elsewhere on the board
QEP1_S: U301.J4 (GPIO22/EQEP1_STROBE); also elsewhere on the board
QEP2_A: U301.K3 (GPIO24/EQEP2_A); also elsewhere on the board
QEP2_B: U301.K2 (GPIO25/EQEP2_B); also elsewhere on the board
QEP2_I: U301.K1 (GPIO26/EQEP2_INDEX); also elsewhere on the board
QEP2_S: U301.L1 (GPIO27/EQEP2_STROBE); also elsewhere on the board
RS485_EN: U301.N16 (GPIO56); also elsewhere on the board
RS485_RX: U301.P19 (GPIO55/SCIB_RX); also elsewhere on the board
RS485_TX: U301.P18 (GPIO54/SCIB_TX); also elsewhere on the board
RUN_LED0: U301.U14 (GPIO34); also elsewhere on the board
RUN_LED1: U301.T14 (GPIO35); also elsewhere on the board
SCIA_RX: U301.V11 (GPIO28/SCIA_RX); also elsewhere on the board
SCIA_TX: U301.W11 (GPIO29/SCIA_TX); also elsewhere on the board
SD_A1: U301.V16 (GPIO36/SD1_D1); also elsewhere on the board
SD_A2: U301.U16 (GPIO37/SD1_D2); also elsewhere on the board
SD_A3: U301.T16 (GPIO38/SD1_D3); also elsewhere on the board
SD_A4: U301.W17 (GPIO39/SD1_D4); also elsewhere on the board
SD_A_CLK: U301.E2 (GPIO17/SD1_C1); also elsewhere on the board
SD_B1: U301.R17 (GPIO49/SD2_D1); also elsewhere on the board
SD_B2: U301.R18 (GPIO50/SD2_D2); also elsewhere on the board
SD_B3: U301.R19 (GPIO51/SD2_D3); also elsewhere on the board
SD_B4: U301.P16 (GPIO52/SD2_D4); also elsewhere on the board
SD_B_CLK: U301.N18 (GPIO57/SD2_C1); also elsewhere on the board
STEP1: U301.B19 (GPIO67); also elsewhere on the board
STEP2: U301.B18 (GPIO69); also elsewhere on the board
USB_D+: U301.C19 (GPIO43/USB0DP); also elsewhere on the board
USB_D-: U301.D19 (GPIO42/USB0DM); also elsewhere on the board

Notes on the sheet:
SD C2/3/4 goes directly inside uC only and MUST C1 required
one PWM channel for all 8 SD
Sdefault gpio's for sciA boot, don't move
SD C2/3/4 goes directly inside uC only and MUST C1 required
I've spend hours to choose the GPIO's for each interfase trying to not crash one to the other, just pay attemtion if you wanna move some pieces... I've used global labels connector to go from one page to another instead the off-page connector because it's more proune to errors.. I know that is not 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
uC GPIO's pins

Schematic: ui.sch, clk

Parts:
C1401: 1nF; C_0603_1608Metric
C1402, C1403, C1405: 10u; C_0603_1608Metric
C1404: 1uF; C_0603_1608Metric
D1401, D1402: red@2mA; LED_0603_1608Metric
J1401: NHD-4.3-480272FT-CTXL-T; HD-4.3-480272
J1402: Conn_01x02; Molex_KK-254_AE-6410-02A_1x02_P2.54mm_Vertical
R1401, R1402: 680; R_0603_1608Metric
R1403: 680e; R_0603_1608Metric
R1404: 220e; R_0603_1608Metric
SW1403, SW1404: SW_Push; SW_SPST_PTS645
U1401: PAM8301; SOT-23-6

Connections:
3V3: J1401.1, R1401.1, R1402.1; also elsewhere on the board
5VC: C1402.1, C1403.1, C1405.1, J1401.17, J1401.18, U1401.5 (VDD); also elsewhere on the board
GND: C1401.1, C1402.2 (Capacitor), C1403.2 (Capacitor), C1405.2 (Capacitor), J1401.2, J1401.19, J1401.20, SW1403.2, SW1404.2, U1401.2 (GND), U1401.4 (~SD); also elsewhere on the board
LCD_AUDIO: J1401.9, R1403.1; also elsewhere on the board
LCD_GPIO0: J1401.11; also elsewhere on the board
LCD_GPIO1: J1401.12; also elsewhere on the board
LCD_GPIO2: J1401.13; also elsewhere on the board
LCD_GPIO3: J1401.14; also elsewhere on the board
LCD_GPIO4: J1401.15, SW1403.1; also elsewhere on the board
LCD_GPIO5: J1401.16, SW1404.1; also elsewhere on the board
LCD_INT: J1401.7; also elsewhere on the board
LCD_SPI_CLK: J1401.3; also elsewhere on the board
LCD_SPI_CS: J1401.6; also elsewhere on the board
LCD_SPI_MISO: J1401.4; also elsewhere on the board
LCD_SPI_MOSI: J1401.5; also elsewhere on the board
LCD_SPI_PDW: J1401.8; also elsewhere on the board
unnamed: C1401.2 (Capacitor), R1403.2, R1404.1
unnamed: C1404.1, R1404.2
unnamed: C1404.2 (Capacitor), U1401.3 (IN)
unnamed: D1401.2 (A), R1401.2
unnamed: D1402.2 (A), R1402.2
unnamed: J1402.1, U1401.6 (OUT+)
unnamed: J1402.2, U1401.1 (OUT-)
RUN_LED0: D1401.1 (K); also elsewhere on the board
RUN_LED1: D1402.1 (K); also elsewhere on the board

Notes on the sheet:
Multipropouse LEDs
to optionally connect a speaker uggly instead of a buzzer
LCD UI interfase
interfase directly using f20 wires flat cable for NHD-4.3-480272FT-CTXL-T newheaven LCD or hand wiring EA eDIP128B-6LWTP or using any paralel 8080 3v3 interfase bitbanging the SPI and GPIO pins
backligth supply
I leave 4 push buttons as an alternative to touch pannel LCD, but also in case the some internal configuration has to be made without UI, or for debg. I think is not the best to use them as UI directly over the main board, for isolation and mechanicall isues.. better to do another board of leds and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
I leve a multi LCD/Touch/button 20 pins IDC connector to interfase with some UI. It could be simple leds,, a character LCD or an EVE graphic LCD as I recomment 'cause for same price you've all in one piece and it's already done, clean, usefull and intuitive interfase. I've added 2 more GPIO's 4 and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
for bulk capacitor

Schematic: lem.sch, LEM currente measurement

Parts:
C1501, C1502, C1509, C1513, C1514, C1515: 100pF; C_0603_1608Metric
C1504, C1505, C1508, C1510, C1511, C1512: 100nF; C_0603_1608Metric
J1501, J1502, J1503, J1504, J1505, J1506: tblock2x3; tblock02x03
R1501, R1503, R1505, R1507, R1509, R1511: 5k; R_0603_1608Metric
R1502, R1504, R1506, R1508, R1510, R1512: 3.3k; R_0603_1608Metric
U1501, U1502, U1503, U1504, U1505, U1506: LXS6-NPS; LEM_LTSR-NP

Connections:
5VC: C1504.2 (Capacitor), C1505.2 (Capacitor), C1508.2 (Capacitor), C1510.2 (Capacitor), C1511.2 (Capacitor), C1512.2 (Capacitor), U1501.9 (5V), U1502.9 (5V), U1503.9 (5V), U1504.9 (5V), U1505.9 (5V), U1506.9 (5V); also elsewhere on the board
/lem/LemAU_1: J1503.3, U1503.1 (IN1)
/lem/LemAU_2: J1503.5, U1503.2 (IN2)
/lem/LemAU_3: J1503.4, U1503.3 (IN3)
/lem/LemAU_4: J1503.1, U1503.4 (OUT4)
/lem/LemAU_5: J1503.2, U1503.5 (OUT5)
/lem/LemAU_6: J1503.6, U1503.6 (OUT6)
/lem/LemAV_1: J1501.3, U1501.1 (IN1)
/lem/LemAV_2: J1501.5, U1501.2 (IN2)
/lem/LemAV_3: J1501.4, U1501.3 (IN3)
/lem/LemAV_4: J1501.1, U1501.4 (OUT4)
/lem/LemAV_5: J1501.2, U1501.5 (OUT5)
/lem/LemAV_6: J1501.6, U1501.6 (OUT6)
/lem/LemA_All_1: J1502.3, U1502.1 (IN1)
/lem/LemA_All_2: J1502.5, U1502.2 (IN2)
/lem/LemA_All_3: J1502.4, U1502.3 (IN3)
/lem/LemA_All_4: J1502.1, U1502.4 (OUT4)
/lem/LemA_All_5: J1502.2, U1502.5 (OUT5)
/lem/LemA_All_6: J1502.6, U1502.6 (OUT6)
/lem/LemBU_1: J1504.3, U1504.1 (IN1)
/lem/LemBU_2: J1504.5, U1504.2 (IN2)
/lem/LemBU_3: J1504.4, U1504.3 (IN3)
/lem/LemBU_4: J1504.1, U1504.4 (OUT4)
/lem/LemBU_5: J1504.2, U1504.5 (OUT5)
/lem/LemBU_6: J1504.6, U1504.6 (OUT6)
/lem/LemBV_1: J1505.3, U1505.1 (IN1)
/lem/LemBV_2: J1505.5, U1505.2 (IN2)
/lem/LemBV_3: J1505.4, U1505.3 (IN3)
/lem/LemBV_4: J1505.1, U1505.4 (OUT4)
/lem/LemBV_5: J1505.2, U1505.5 (OUT5)
/lem/LemBV_6: J1505.6, U1505.6 (OUT6)
/lem/LemB_All_1: J1506.3, U1506.1 (IN1)
/lem/LemB_All_2: J1506.5, U1506.2 (IN2)
/lem/LemB_All_3: J1506.4, U1506.3 (IN3)
/lem/LemB_All_4: J1506.1, U1506.4 (OUT4)
/lem/LemB_All_5: J1506.2, U1506.5 (OUT5)
/lem/LemB_All_6: J1506.6, U1506.6 (OUT6)
GND: C1501.1, C1502.1, C1504.1, C1505.1, C1508.1, C1509.1, C1510.1, C1511.1, C1512.1, C1513.1, C1514.1, C1515.1, R1502.2, R1504.2, R1506.2, R1508.2, R1510.2, R1512.2, U1501.8 (GND), U1502.8 (GND), U1503.8 (GND), U1504.8 (GND), U1505.8 (GND), U1506.8 (GND); also elsewhere on the board
LEM_A_ALL: C1502.2 (Capacitor), R1503.2, R1504.1; also elsewhere on the board
LEM_A_U: C1509.2 (Capacitor), R1505.2, R1506.1; also elsewhere on the board
LEM_A_V: C1501.2 (Capacitor), R1501.2, R1502.1; also elsewhere on the board
LEM_B_ALL: C1515.2 (Capacitor), R1511.2, R1512.1; also elsewhere on the board
LEM_B_U: C1513.2 (Capacitor), R1507.2, R1508.1; also elsewhere on the board
LEM_B_V: C1514.2 (Capacitor), R1509.2, R1510.1; also elsewhere on the board
unnamed: R1501.1, U1501.7 (Out)
unnamed: R1503.1, U1502.7 (Out)
unnamed: R1505.1, U1503.7 (Out)
unnamed: R1507.1, U1504.7 (Out)
unnamed: R1509.1, U1505.7 (Out)
unnamed: R1511.1, U1506.7 (Out)

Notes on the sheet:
with 6 screw connector you could choose 3 range of current measurement 1x, 2x or 3x. IN 1 BRIDGE 1-2-3 and 4-5-6 OUT 4 ------- X IN 1 BRIDGE 1-2 and 3-5-6 OUT 4 ------- 2X IN 1 BRIDGE 2-6 and 3-5 OUT 4 ------- 3X
8 LEM's current measurement U+V+W+ALL x 2
The intention of these lems is to have the capacity on the control board to measure all the current, without the need of the sigma delta chips on power board side. Why?? becouse I've study the two options carrefullty and I've conclude that there are very similar, and more or less buck per byck (a l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
I've decided to eliminate 1 LEM, you could use 3 in line measurement, or 2 in line plus one for all. De reason is size of board and complexity
chanlog1: I've decided to return to a 2x3 terminal block output 'cause it match the size of the LEM

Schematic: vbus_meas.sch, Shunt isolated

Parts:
C1601, C1602, C1603, C1604, C1607, C1608, C1609, C1610: 100nF; C_0603_1608Metric
C1605, C1606: 330p; C_0603_1608Metric
L1601, L1602, L1603, L1604: L_Small; L_1206_3216Metric_Pad1.42x1.75mm_HandSolder
R1601, R1602, R1603, R1604, R1605, R1606: 12e; R_0603_1608Metric
R1607, R1608, R1609, R1610: 1k; R_0603_1608Metric
R1611, R1612, R1613, R1614, R1615, R1616, R1617, R1618: 1M; R_1206_3216Metric_Pad1.42x1.75mm_HandSolder
U1601, U1602: AMC1311B; SSO-8_6.8x5.9mm_P1.27mm_Clearance8mm
U1603, U1604: RFM-0505S; rfm0505
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

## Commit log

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2019-11-07 add first kicad schematics converted from Altimum
    after converting files from the last ethercat controlboard from altium
    to kicad, I'm working on recontruct the files, organize the .libs
    unified on servo.lib and in learning and deciding what to add and what
    to forget in the way... a long way
    [ethernet.sch, gpio.sch, servo.sch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]
2019-11-07 solve a broken link to schematics1.jpg on README
2019-11-07 adc added but not checked yest.. i
    adc deserves a special attention becouse we don't want so much channels,
    nor differential input.. neither so much references..
    [adc.sch, ethernet.sch, gpio.sch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]
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2019-11-17 datasheets added, I'll remove usb interface completely
    I've decided to remove the jtag and isolation interface completely
    maybe next I'll add some rs485 isolation interfase for debug, but for
    now, it's not neccesary 'cose I'd use a jtag isolated interface
    exclusively for that
    [ethercat.sch, servo.sch, usb_emulator.sch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]
2019-11-17 usb interface changed by emu_interface
    I've cleaned all the jtag interface, so the only things that go out is
    jtag HOT and rx/tx isolated. I left the isolator for rx/tx cose I'm
    planning to add rs485 using the same isolator and regulator, if not, I'd
    clean these IC's also
    [adc.sch, emu_interface.sch, ethercat.sch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]
2019-11-18 power.sch added with new power 1V2, 3V3, an so global labels
    I've added the power schematic and try to ojin the power label as 3V3,
    VDD_3V3 an so.. keep going
    [adc.sch, emu_interface.sch, ethercat.sch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]
2019-11-18 added README pics, and keep going on power sch
    I've been deleting some unused IC's and accomodating libs, also add some
    pics to README
    [ethercat.sch, ethernet.sch, power.sch]
2019-11-20 clk.sch added. I'm seeing what to delete and what to keep
    I've added clk.sch clk related schematics, so I'm looking to clean up
    the design 'cose it has a lot of things not used in the actual design
    [adc.sch, clk.sch, emu_interface.sch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]
2019-11-20 cleaned clk.sch and some details on ethercat/net
    I've cleaned up a lot from clk, I'm planning to use 25mhz external clk
    and the ethernet/cat interfaces will eat from C2000, not from same clk.
    I think it could work, cose the uC is designed in that way to use
    GPIO154 to provide the clk.. will see...
    [adc.sch, clk.sch, emu_interface.sch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]
2019-11-22 cleaning power, added ac/dc to 15v
    I've added the ac/dc power supply based on encapsulated off load power
    supply and chainde linear regulator for 5, 3v3 and 1v2 for cold gnd and
    5v and 3v3 for hot gnd.
    I'll next join some sheet 'cose some of those are almost empty
    [ac_input.sch, adc.sch, clk.sch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]
2019-11-25 ok, it's enough cleaned to mix with power interface
    I think it's time to mix with power interfaces.. It's enough cleaned
    [ac_input.sch, adc.sch, clk.sch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]
2019-11-26 added igbt interface, lem, and impprove root page
    improved root page, added lem using hall sensor instead shunt, add
    somthing on adc page, and ac input.. keep working
    [ac_in.sch, adc.sch, clk.sch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]
2019-12-01 I've connected interfaces to gpio and change some muxes
    I've changed some muxes reading the datasheet to group same kind of
    signals, now it's time to add encoders input
    [ac_in.sch, adc.sch, clk.sch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]
2019-12-02 added can, rs485, qep endat and others details
    I've added a lot of interfases and route his pins to gpios... keep going
    [ac_in.sch, adc.sch, can.sch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]
2019-12-02 added shunt using sigma delta, just fot 1 channel
    I've added a sigma delta isolated sampler for use with shunt in phase
    measurement. 'cose it seems is the best accuracy method for current
    measurement, but it implies a lot of componentes, 8 PWM lines to
    generate the sigma delta clk, or maybe I'd use only one clk for all
    sigma deltas, ..I've to think about it, but it seems that should be
    better than Hall.. working on that
    [ac_in.sch, adc.sch, can.sch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]
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2019-12-02 Added diff adc isolated to add more adc channels
    I've added isolated adc's ACM1100 in adition of ACM1304, 'cose C2000
    only has 4 sigmadelta filter, and for 2 motors I need 6 for phase
    measurement and 1 for BUS voltage measurement. So I'll have to decide if
    I eliminate the hall sensores, becosue, using 7 isolated diff adc plus 4
    sigma delta is enough to the requeriments... or instead eliminate all
    sigma delta too and left only adc diff isolated.. I think these will be
    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
    [ac_in.sch, adc.sch, can.sch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]
2019-12-26 Come back to moldova to finish schematics and begin layout
    I've started again from Moldova to discuss with Alexander the details.
    I'm now working with schematics requeriments.
    [ac_in.sch, adc.sch, can.sch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]
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2020-01-09 remove isolation GPIO's and replace it by free pins at IGBT
    I remove completely the isolated inputs pins cause I've 8 pins free at
    IGBT isolated interfase, so I leave 4 for outpus and 4 for inputs with
    one isolated stage, the same as the previous isolated GPIO sheet..
    I've improved the DBG sheet and some other details,. I'm ready to make
    some electrical checks and fchoose the parts codes and footprints.. go
    for it!
    [ac_in.sch, can.sch, endat.sch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]
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2020-01-17 changed 200mils connector to 150mils 'cause space constraints
    I've decided to change 200 mils input connector for encat, rs485 and so
    for 150mis 'cose it doesn't deliver so much current and I'd save some
    space in the board. I've added the step/dir differential interface that
    I've fotgot, and also add differential input to all signals of
    incremental encoder interface A/B/I/S .. now lets rock
    [ac_in.sch, can_485.sch, endat.sch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]
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2020-02-19 begining error checker on PCB
    [igbt.sch]
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2020-03-23 fixing the manufacturer issues, and regenerate gerbers and BOM
    I've changed boostrap resistors from 0805 to 0603 'cause now I've a
    bridge to choose how to boot, and nothing to solder or desolder.
    And I've changed pin header to IDC12 for debug connector.
    [EQ_20031662A.xlsx, SBH11-_ _ _C-D06-SM-_ _.STEP, ac_in.sch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]
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
